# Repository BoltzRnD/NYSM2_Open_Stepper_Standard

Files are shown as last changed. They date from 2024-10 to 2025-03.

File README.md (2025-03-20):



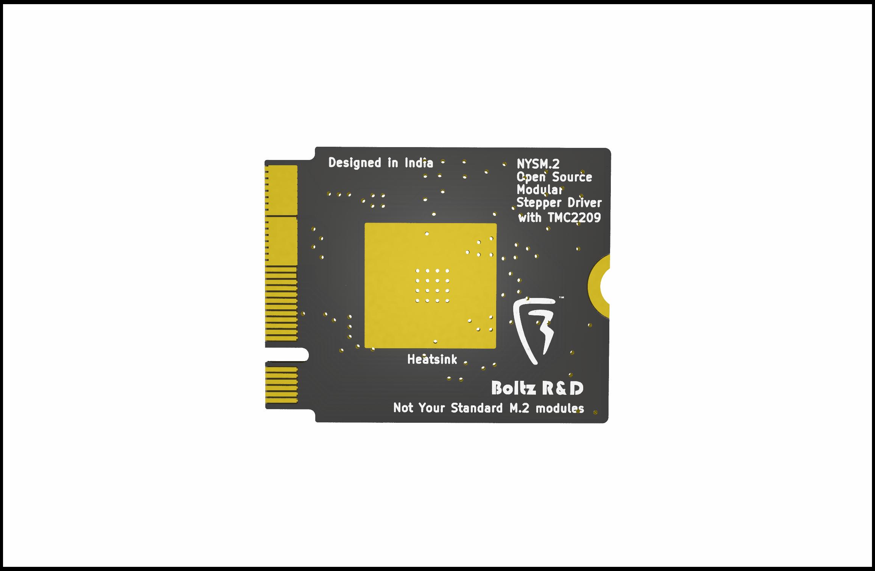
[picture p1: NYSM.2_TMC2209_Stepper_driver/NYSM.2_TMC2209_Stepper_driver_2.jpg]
NYSM.2


# NYSM.2 Open Stepper Standard
## Not Your Standard M.2
### "Not Your Standard M.2" is literally not your standard m.2 interface, and is a new open-source stepper motor driver board that utilizes the M.2 interface to control motors using the TMCxx and all other stepper drivers.

Modular stepper drivers are far superior than traditional pololu footprints as it has

1. Poka-yoke installations: The Key's in the interfaces makes sure that you never mess up installation orientations of the driver

apart from this NYSM.2 extends beyond these to provide more features as below:

1. physical locking mechanisms: to make sure drivers are locked in when In operation.

2. Horizontal installation: instead of vertical mounting, to not only save space in Z axis, but to also make the system less fragile to accidental damage if stuck by a physical shock.

3. Top and Bottom Installations: since NYSM.2 utilizes SMD and single layer mounted connectors, it means that it is possible to add by design 2 NYSM.2 modules in the same footprint area, drastically reducing the required footprint for more drivers - i.e - 20 drivers in 10 drivers area by installing 10 on top layer and 10 on bottom.

4. highly cost effective: since M.2 is a widely available standard with high MOQs already flooding the industry, the M.2 connectors can be integrated at very low costs into your design, where the stepper card doesn't even need a connector as it uses an edge connector built into the PCB only. in comparison to other modular standards that uses custom repurposed obsolete connector that has low manufacturing volumes. With NYSM.2 we can adopt a modular standard at almost same cost of a traditional pololu stepper drivers.

5. Powerful in terms of power: NYSM.2 utilizes 8 contacts(0.5A per pin) per power connection to deliver a whopping **4A** to the motors, that too at **24V**, that totals to **96W** per driver.
moreover it is theoretically possible to get more power out of it by increasing the voltages.

But that is not the best thing about NYSM.2 standard, the only best thing about it is only and only it's open source nature and GPL V3 license, that allows creators, hobbyist and manufacturers worldwide to move to a new and open modular stepper driver interface standard.
unlike other modular stepper interfaces, this interface is open inside out, and is not designed to lock you into single specific manufacturer's ecosystem. and is made for the world to use.

## The NYSM.2 Standard Pinout Format

## Pinout Table

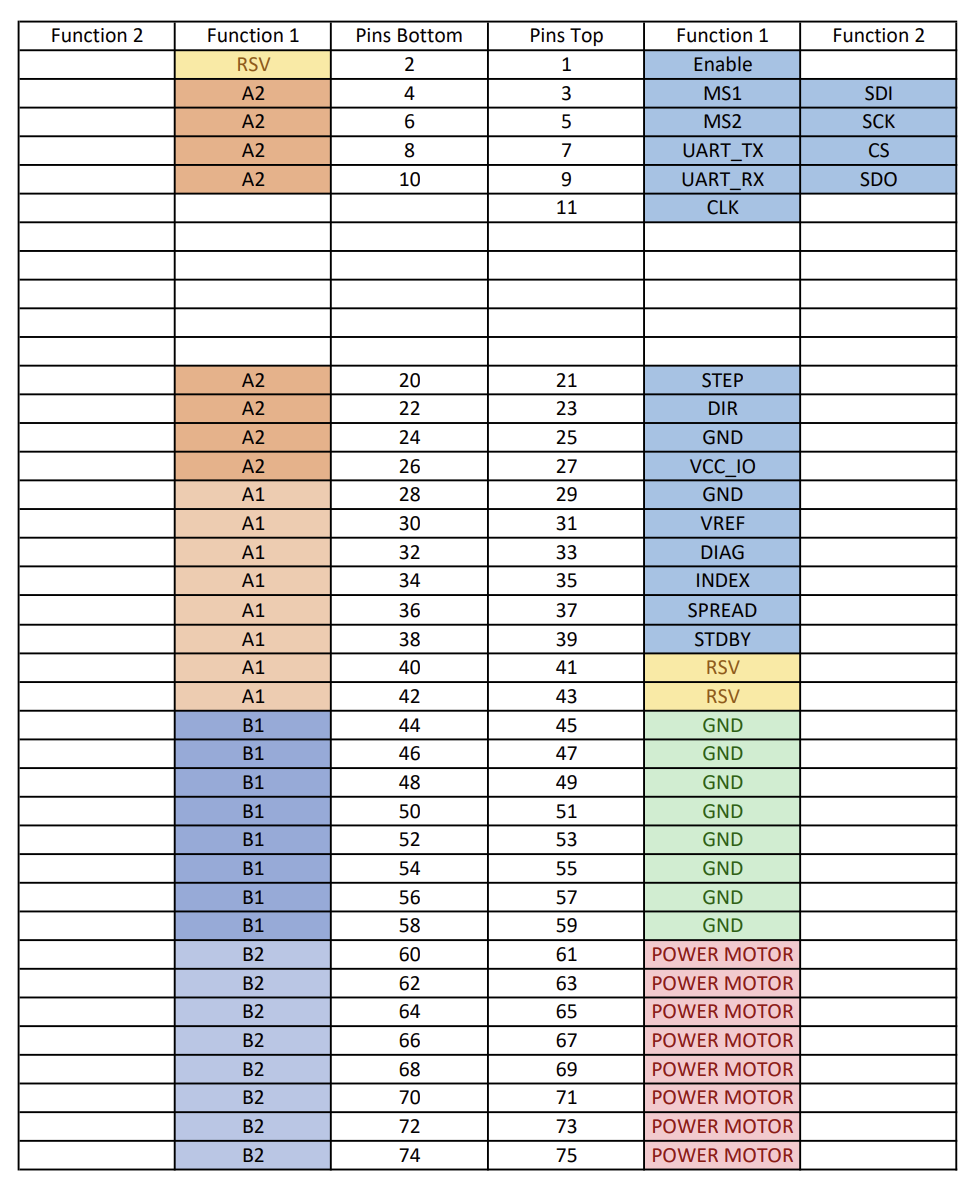
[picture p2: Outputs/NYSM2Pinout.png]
NYSM.2 Pinout


| Pin Name | Pin Number | Description 
|---|---|---|
| EN | 1 | Enable/Disable Stepper Driver
| MS1 | 3 | Microstep Selection Pin 1 / CFG1 / SDI
| MS2 | 5 | Microstep Selection Pin 2 / CFG2 / SCK
| UART_TX | 7 | UART Transmission (Communication) / CFG 3 / CS
| UART_RX | 9 | UART Receive (Communication) / CFG0 / SDO
| CLK | 11 | CLK input 
| STEP | 21 | STEP input 
| DIR | 23 | DIR input 
| GND | 25 | Ground 
| VCC_IO | 27 | 3.3V to 5V IO supply voltage for all digital pins (does not supply IC logic part).
| GND | 29 | Ground 
| VREF | 31 | Analog reference voltage for current scaling or reference current for use of internal sense resistors
| DIAG | 33 | Diagnostic and StallGuard output
| INDEX | 35 | Configurable index output. Provides index pulse.
| SPREAD | 37 | Chopper mode selection: Low=StealthChop, High=SpreadCycle (may be left unconnected)
| STDBY | 39 | STANDBY input  
| GND | 45, 47, 49, 51, 53, 55, 57, 59 | Ground/PSU Negative (0.5A per pin, 4A Total)
| POW_MOT | 61, 63, 65, 67, 69, 71, 73, 75 | Motor supply voltage (0.5A per pin, 4A Total)
| A2 | 4, 6, 8, 10, 20, 22, 24, 26 | Motor coil A output 2 (0.5A per pin, 4A Total)
| A1 | 28, 30, 32, 34, 36, 38, 40, 42 | Motor coil A output 1 (0.5A per pin, 4A Total)
| B1 | 44, 46, 48, 50, 52, 54, 56, 58 | Motor coil B output 1 (0.5A per pin, 4A Total)
| B2 | 60, 62, 64, 66, 68, 70, 72, 74 | Motor coil B output 2 (0.5A per pin, 4A Total)

# Manufacturing and other design considerations

Please take special care to follow these points when manufacturing the NYSM2 Boards
1. Board Thickness - 0.8mm (Standard M.2 Board Thickness)
2. Gold Plating is preferred but not Necessary.
3. This Version of the board omits the use of current limit series phase resistors, in case it is a necessity for your design, Please use the design from Branch alt_sense
4. Short The onboard jumper to use the potentiometer for standalone mode.
5. Use a generic Raspberry Pi or other 25x25mm heatsinks on top.

# License
NYSM.2 standard pinout and NYSM.2 TMC2209 Board contributed by Boltz R&D is licensed under GPL V3 license, and is owned by the community and everyone.
Also while the standard is open(i.e - The standard pinout sequence on M.2 Key B and it's derivatives only, that means proprietary manufacturers needs to be compliant to GPLV3 for only the pinout.),
you can integrate it into your proprietary designs as long as the NYSM.2 section of your design respects the license.
We invite all creators, hobbyist, and manufacturers to utilize the standard and the design.

# Key Features for this NYSM.2 TMC2209 Board:
* NYSM.2 Interface: Compact, modular design that fits into M.2 slots, making it easy to install and maintain.
* TMC2209 Stepper Driver: One of the Industry-leading drivers for stepper motors, featuring sensorless homing, stall detection, and ultra-quiet operation.

## Assembly and Setup

1. **Step 1**: Insert the **NYSM.2** board into an M.2 slot.
2. **Step 2**: Connect your stepper motor wires to the appropriate output terminals.
3. **Step 3**: Configure your firmware (e.g., **Marlin** or **Klipper**) to control the TMC2209 driver.
4. **Step 4**: Power on the system, and your motors are ready.

## Getting Started on Development:

Clone the repository:  
`git clone https://github.com/BoltzRnD/NYSM2_Open_Stepper_Standard`

# Join the Community
We are actively looking for contributors to help us enhance this project. You can join our community to discuss ideas, report bugs, or request features:

- **Discord**: [Join us here](https://discord.gg/xWGaHd83Hs)
- **Email**: info@boltzrnd.com

# Future Plans
- **Custom Heatsink Designs**.
- **Extended Compatibility**: support for other stepper driver like TMC5160 and TMC2130.

# Disclaimer
The **NYSM.2 standard and NYSM.2 board** is provided as-is without any warranties. Boltz R&D is not responsible for any damages or issues that may arise from the use of this board.

    NYSM.2 standard
    Copyright (C) 2024 Boltz R&D

    This Project/Open Standard is free: you can redistribute it and/or modify
    it under the terms of the GNU General Public License as published by
    the Free Software Foundation, either version 3 of the License, or
    (at your option) any later version.

    This is distributed in the hope that it will be useful,
    but WITHOUT ANY WARRANTY; without even the implied warranty of
    MERCHANTABILITY or FITNESS FOR A PARTICULAR PURPOSE.  See the
    GNU General Public License for more details.

    You should have received a copy of the GNU General Public License
    along with this program.  If not, see <https://www.gnu.org/licenses/>.

Contact : info@boltzrnd.com

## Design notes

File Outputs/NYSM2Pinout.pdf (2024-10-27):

Function 2 | Function 1 | Pins Bottom | Pins Top | Function 1 | Function 2
| RSV | 2 | 1 | Enable
| A2 | 4 | 3 | MS1 | SDI
| A2 | 6 | 5 | MS2 | SCK
| A2 | 8 | 7 | UART_TX | CS
| A2 | 10 | 9 | UART_RX | SDO
| | | 11 CLK
A2 | 20 | 21 | STEP
A2 | 22 | 23 | DIR
A2 | 24 | 25 | GND
A2 | 26 | 27 | VCC_IO
A1 | 28 | 29 | GND
A1 | 30 | 31 | VREF
A1 | 32 | 33 | DIAG
A1 | 34 | 35 | INDEX
A1 | 36 | 37 | SPREAD
A1 | 38 | 39 | STDBY
A1 | 40 | 41 | RSV
A1 | 42 | 43 | RSV
B1 | 44 | 45 | GND
B1 | 46 | 47 | GND
B1 | 48 | 49 | GND
B1 | 50 | 51 | GND
B1 | 52 | 53 | GND
B1 | 54 | 55 | GND
B1 | 56 | 57 | GND
B1 | 58 | 59 | GND
B2 | 60 | 61 | POWER MOTOR
B2 | 62 | 63 | POWER MOTOR
B2 | 64 | 65 | POWER MOTOR
B2 | 66 | 67 | POWER MOTOR
B2 | 68 | 69 | POWER MOTOR
B2 | 70 | 71 | POWER MOTOR
B2 | 72 | 73 | POWER MOTOR
B2 | 74 | 75 | POWER MOTOR

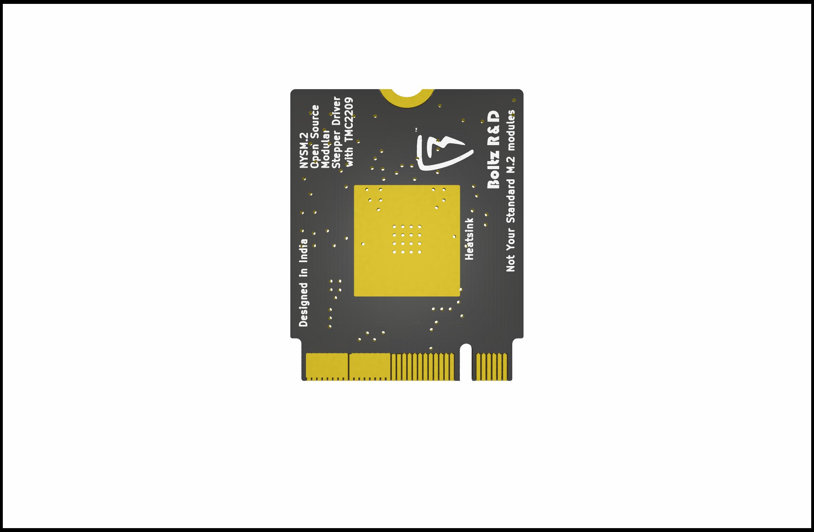
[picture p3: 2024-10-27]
NYSM.2_TMC2209_Stepper_driver/NYSM.2_TMC2209_Stepper_driver.jpg

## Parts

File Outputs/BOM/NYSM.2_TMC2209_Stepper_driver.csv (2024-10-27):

Designator | Comment | Footprint | Qty | DNP | JLCPCB Part #（optiona | Manufacturer_Part_Number
C1 | 22nF/50V | Capacitor_SMD:C_0402_1005Metric | 1 |  | C107026 | CC0402KRX7R9BB223
C2 | 100nF/50V | Capacitor_SMD:C_0402_1005Metric | 1 |  | C152814 | 0402B104K500CT
C6 | 100nF/50V | Capacitor_SMD:C_0402_1005Metric | 1 |  | C152814 | 0402B104K500CT
C7 | 4.7uF 10V | Capacitor_SMD:C_0402_1005Metric | 1 |  | C368809 | CL05A475KP5NRNC
C8 | 1uF/50V | Capacitor_SMD:C_0402_1005Metric | 1 |  | C1518208 | GRM155R61H105KE05D
C9 | 100nF/50V | Capacitor_SMD:C_0402_1005Metric | 1 |  | C152814 | 0402B104K500CT
C10 | 100nF/50V | Capacitor_SMD:C_0402_1005Metric | 1 |  | C152814 | 0402B104K500CT
R1 | 20K | Resistor_SMD:R_0402_1005Metric | 1 |  | C384364 | WR04X203JTL
R2 | 20K | Resistor_SMD:R_0402_1005Metric | 1 |  | C384364 | WR04X203JTL
R3 | 1K | Resistor_SMD:R_0402_1005Metric | 1 |  | C163815 | WR04X1001FTL
R6 | 20K | Resistor_SMD:R_0402_1005Metric | 1 |  | C384364 | WR04X203JTL
R7 | 100K | Resistor_SMD:R_0402_1005Metric | 1 |  | C384388 | WR04X104JTL
R8 | NC | Resistor_SMD:R_0402_1005Metric | 1
R9 | NC | Resistor_SMD:R_0402_1005Metric | 1
RV1 | 20K | Potentiometer_SMD:Potentiometer_Bourns_TC33X_Vertical | 1 |  | C128550 | VG039NCHXTB203
U1 | TMC2209 | TMC2209:QFN28_5X5_TRI | 1 |  | C465949 | TMC2209
U2 | M.2-B-KEY | M.2-Templates:M.2-B-KEY | 1

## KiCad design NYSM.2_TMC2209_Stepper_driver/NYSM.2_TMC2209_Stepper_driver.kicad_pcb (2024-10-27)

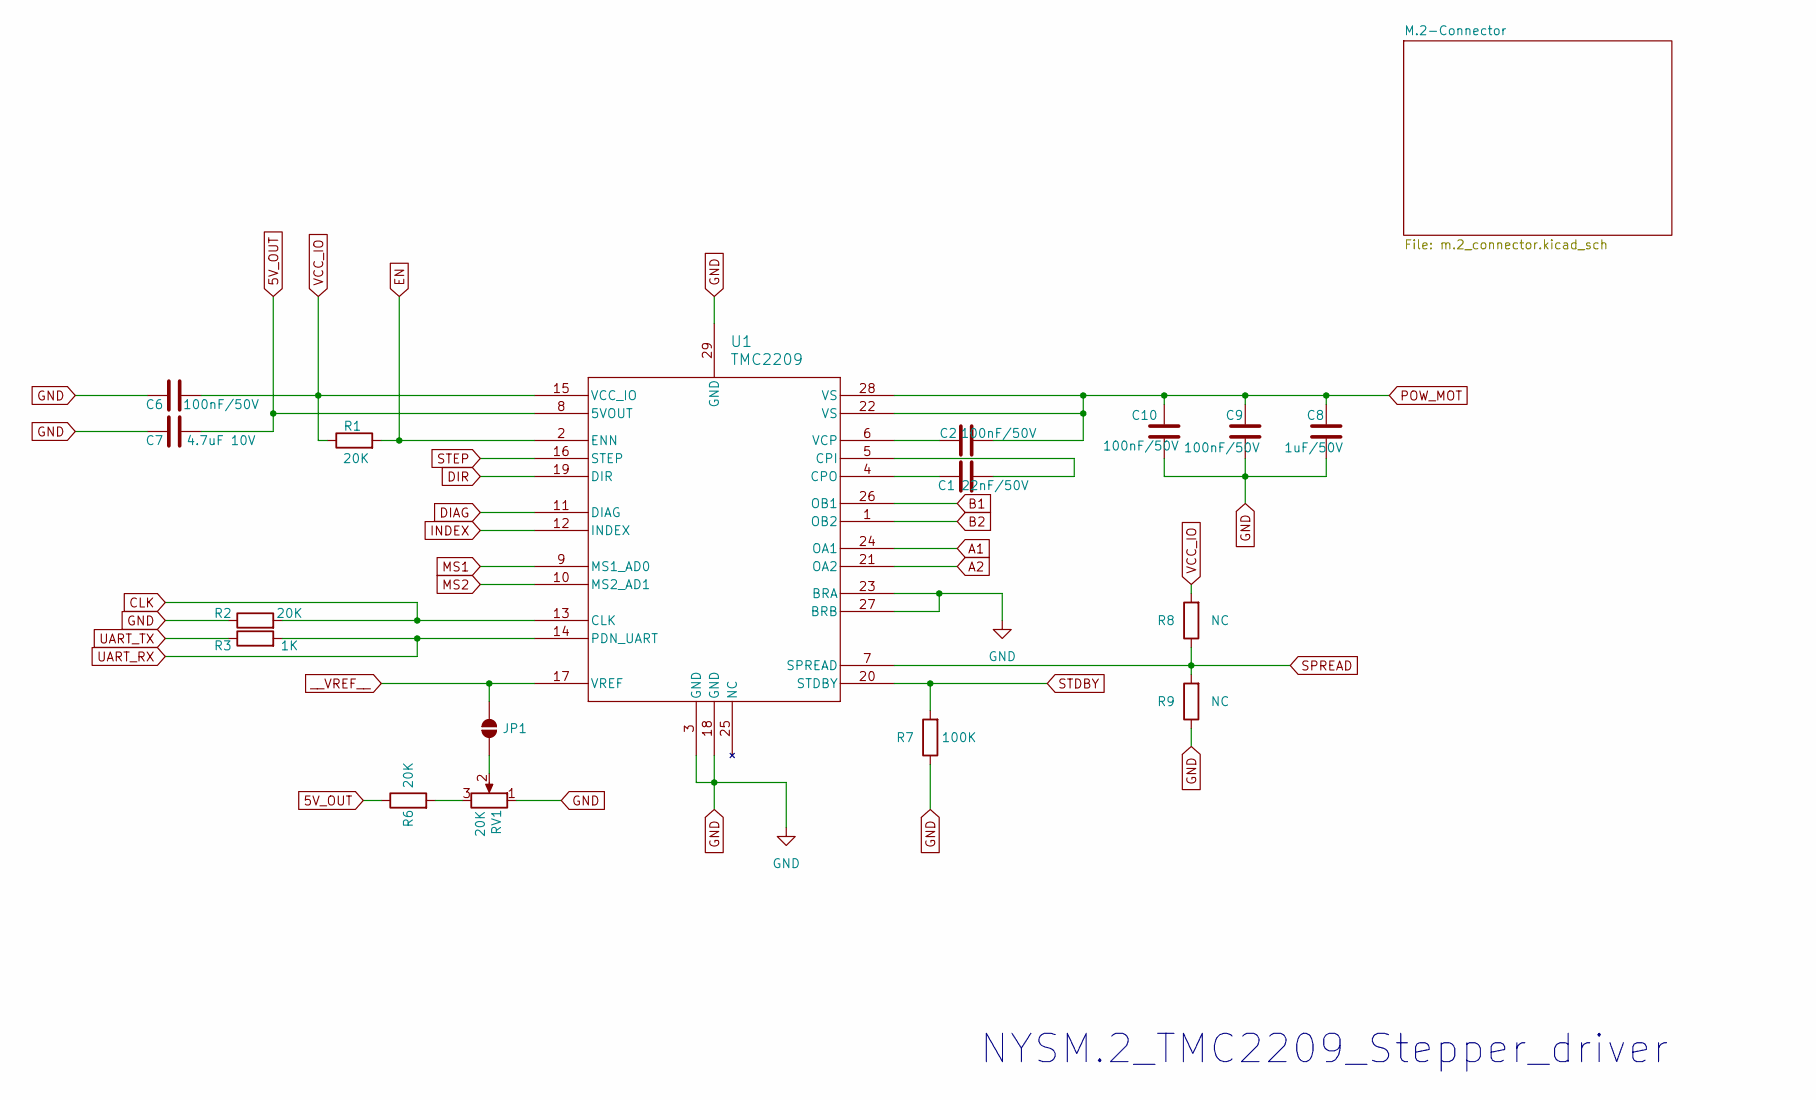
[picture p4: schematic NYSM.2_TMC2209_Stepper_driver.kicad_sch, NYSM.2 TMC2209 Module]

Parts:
C1: 22nF/50V; C_0402_1005Metric; Manufacturer_Part_Number CC0402KRX7R9BB223; LCSC# C107026
C2, C6, C9, C10: 100nF/50V; C_0402_1005Metric; Manufacturer_Part_Number 0402B104K500CT; LCSC# C152814
C7: 4.7uF 10V; C_0402_1005Metric; Manufacturer_Part_Number CL05A475KP5NRNC; LCSC# C368809
C8: 1uF/50V; C_0402_1005Metric; Manufacturer_Part_Number GRM155R61H105KE05D; LCSC# C1518208
JP1: SolderJumper-2_P1.3mm_Open_Pad1.0x1.5mm
R1, R2, R6: 20K; R_0402_1005Metric; Manufacturer_Part_Number WR04X203JTL; LCSC# C384364
R3: 1K; R_0402_1005Metric; Manufacturer_Part_Number WR04X1001FTL; LCSC# C163815
R7: 100K; R_0402_1005Metric; Manufacturer_Part_Number WR04X104JTL; LCSC# C384388
R8, R9: NC; R_0402_1005Metric
RV1: 20K; Potentiometer_Bourns_TC33X_Vertical; Manufacturer_Part_Number VG039NCHXTB203; LCSC# C128550
U1: TMC2209; QFN28_5X5_TRI; Manufacturer_Part_Number TMC2209; LCSC# C465949

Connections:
5V_OUT: C7.2, R6.1, U1.8 (5VOUT)
A1: U1.24 (OA1); also elsewhere on the board
A2: U1.21 (OA2); also elsewhere on the board
B1: U1.26 (OB1); also elsewhere on the board
B2: U1.1 (OB2); also elsewhere on the board
CLK: R2.2, U1.13 (CLK); also elsewhere on the board
DIAG: U1.11 (DIAG); also elsewhere on the board
DIR: U1.19 (DIR); also elsewhere on the board
EN: R1.2, U1.2 (ENN); also elsewhere on the board
GND: C6.1, C7.1, C8.2, C9.2, C10.2, R2.1, R7.1, R9.1, RV1.1, U1.3 (GND), U1.18 (GND), U1.23 (BRA), U1.27 (BRB), U1.29 (GND); also elsewhere on the board
INDEX: U1.12 (INDEX); also elsewhere on the board
MS1: U1.9 (MS1_AD0); also elsewhere on the board
MS2: U1.10 (MS2_AD1); also elsewhere on the board
unnamed: JP1.1 (A), RV1.2
unnamed: R6.2, RV1.3
unnamed: C1.2, U1.5 (CPI)
unnamed: C1.1, U1.4 (CPO)
unnamed: C2.1, U1.6 (VCP)
POW_MOT: C2.2, C8.1, C9.1, C10.1, U1.22 (VS), U1.28 (VS); also elsewhere on the board
SPREAD: R8.1, R9.2, U1.7 (SPREAD); also elsewhere on the board
STDBY: R7.2, U1.20 (STDBY); also elsewhere on the board
STEP: U1.16 (STEP); also elsewhere on the board
UART_RX: R3.2, U1.14 (PDN_UART); also elsewhere on the board
UART_TX: R3.1; also elsewhere on the board
VCC_IO: C6.2, R1.1, R8.2, U1.15 (VCC_IO); also elsewhere on the board
__VREF__: JP1.2 (B), U1.17 (VREF); also elsewhere on the board

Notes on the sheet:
NYSM.2_TMC2209_Stepper_driver

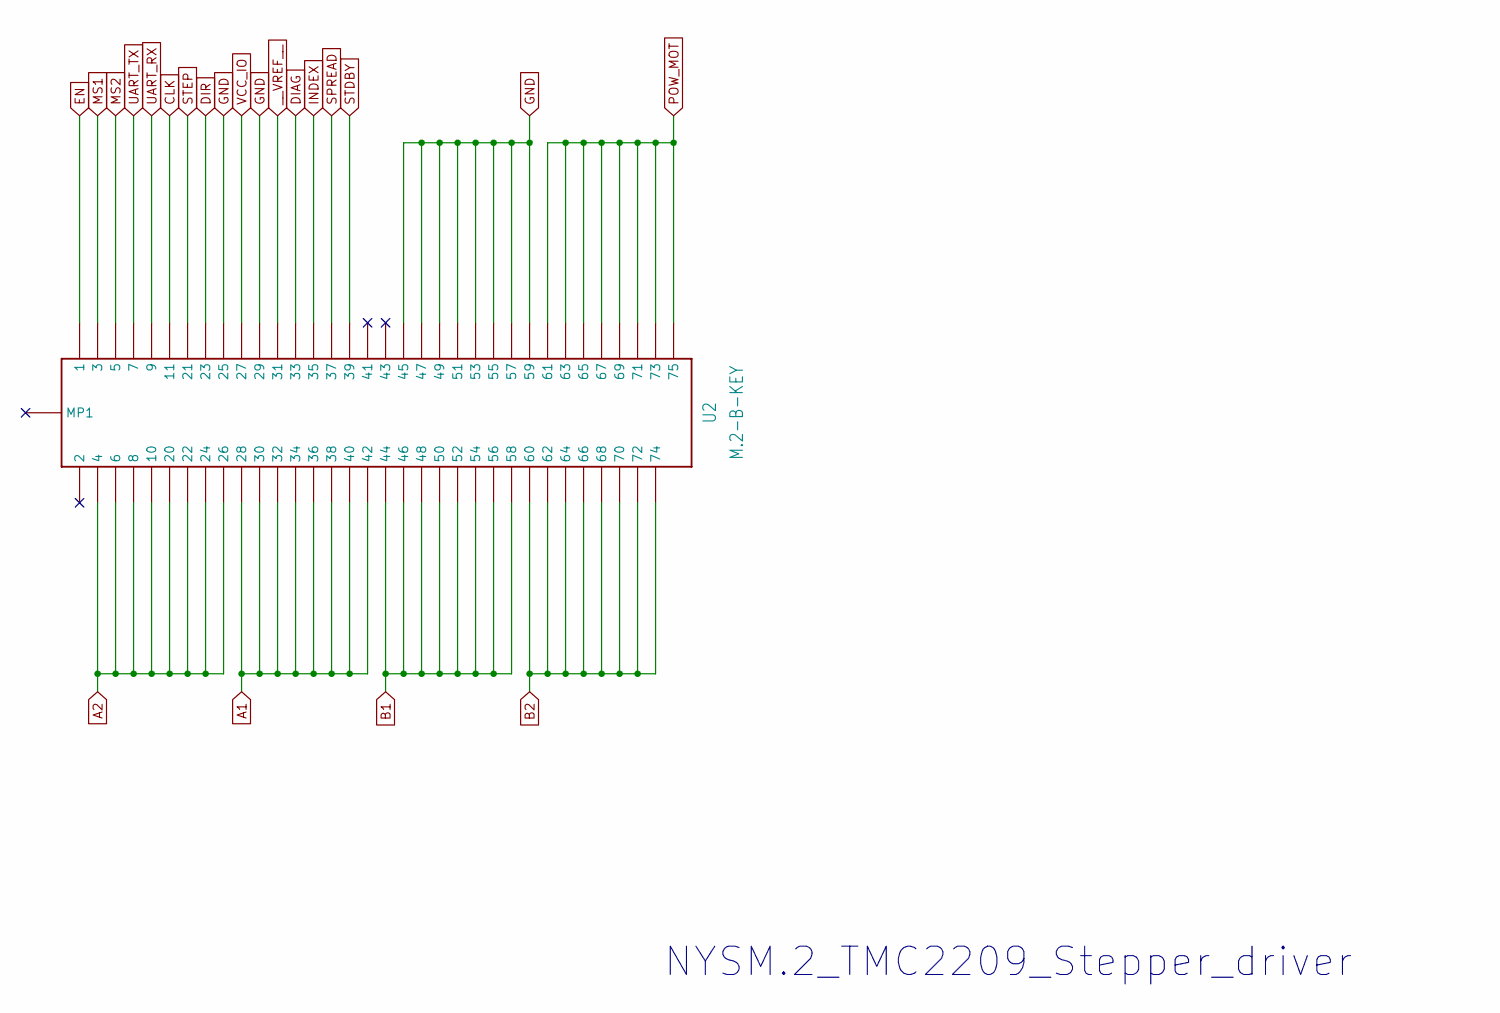
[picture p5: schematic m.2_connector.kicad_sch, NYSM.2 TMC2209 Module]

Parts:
U2: M.2-B-KEY; NYSM2-Card-B-Key

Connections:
A1: U2.P$28 (28), U2.P$30 (30), U2.P$32 (32), U2.P$34 (34), U2.P$36 (36), U2.P$38 (38), U2.P$40 (40), U2.P$42 (42); also elsewhere on the board
A2: U2.P$4 (4), U2.P$6 (6), U2.P$8 (8), U2.P$10 (10), U2.P$20 (20), U2.P$22 (22), U2.P$24 (24), U2.P$26 (26); also elsewhere on the board
B1: U2.P$44 (44), U2.P$46 (46), U2.P$48 (48), U2.P$50 (50), U2.P$52 (52), U2.P$54 (54), U2.P$56 (56), U2.P$58 (58); also elsewhere on the board
B2: U2.P$60 (60), U2.P$62 (62), U2.P$64 (64), U2.P$66 (66), U2.P$68 (68), U2.P$70 (70), U2.P$72 (72), U2.P$74 (74); also elsewhere on the board
CLK: U2.P$11 (11); also elsewhere on the board
DIAG: U2.P$33 (33); also elsewhere on the board
DIR: U2.P$23 (23); also elsewhere on the board
EN: U2.P$1 (1); also elsewhere on the board
GND: U2.P$25 (25), U2.P$29 (29), U2.P$45 (45), U2.P$47 (47), U2.P$49 (49), U2.P$51 (51), U2.P$53 (53), U2.P$55 (55), U2.P$57 (57), U2.P$59 (59); also elsewhere on the board
INDEX: U2.P$35 (35); also elsewhere on the board
MS1: U2.P$3 (3); also elsewhere on the board
MS2: U2.P$5 (5); also elsewhere on the board
POW_MOT: U2.P$61 (61), U2.P$63 (63), U2.P$65 (65), U2.P$67 (67), U2.P$69 (69), U2.P$71 (71), U2.P$73 (73), U2.P$75 (75); also elsewhere on the board
SPREAD: U2.P$37 (37); also elsewhere on the board
STDBY: U2.P$39 (39); also elsewhere on the board
STEP: U2.P$21 (21); also elsewhere on the board
UART_RX: U2.P$9 (9); also elsewhere on the board
UART_TX: U2.P$7 (7); also elsewhere on the board
VCC_IO: U2.P$27 (27); also elsewhere on the board
__VREF__: U2.P$31 (31); also elsewhere on the board

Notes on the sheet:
NYSM.2_TMC2209_Stepper_driver

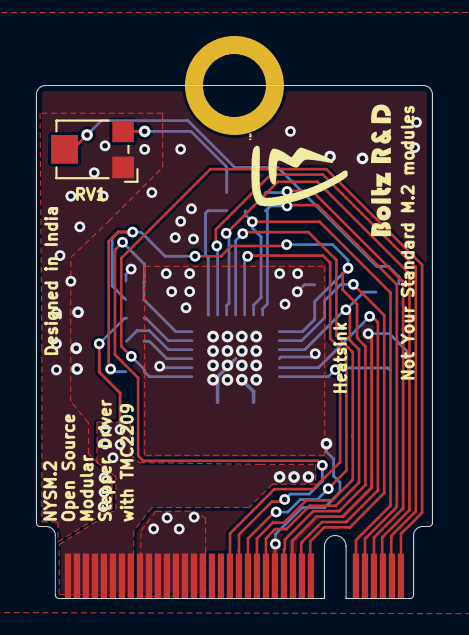
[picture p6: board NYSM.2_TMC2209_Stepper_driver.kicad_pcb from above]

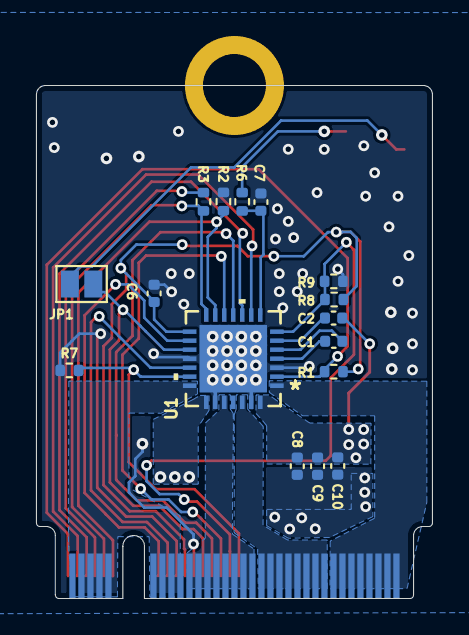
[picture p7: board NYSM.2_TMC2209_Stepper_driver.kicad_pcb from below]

Board: 2 copper layers, 22.0 x 28.5 mm, 18 parts (16 on the bottom side), 26 nets.

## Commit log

2024-10-27 Added Files for Release of NYSM2
    [NYSM.2_TMC2209_Stepper_driver-B_Cu.gbr, NYSM.2_TMC2209_Stepper_driver-B_Mask.gbr, NYSM.2_TMC2209_Stepper_driver-B_Paste.gbr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]
2025-03-20 Update README.md
    info for alternative design with sense resistors
2025-12-21 Add firmware changes for Klipper configuration
    Added firmware changes section with specific configuration details for Klipper and EVAL board.
2025-12-21 Add warning about current limit resistors omission
    Added a warning about the omission of current limit resistors in the board design.

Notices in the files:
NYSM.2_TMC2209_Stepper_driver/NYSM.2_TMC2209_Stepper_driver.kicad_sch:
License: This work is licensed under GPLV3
